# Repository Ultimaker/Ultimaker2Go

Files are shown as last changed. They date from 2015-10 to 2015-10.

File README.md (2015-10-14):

# Ultimaker2Go

Bill of Materials and parts for Ultimaker2Go

In this repository you will find the documentation and source files for all parts in the Ultimaker2Go 3D printer. In the Bill Of Materials (BOM) repository all the parts are numbered and named with the correct amounts. Every part has a separate directory containing all the relevant files. 

The electronic files can be found in the directory 1249 Ulticontroller board and 1546 Ultimainboard V2.1.4.

If you are missing a part or information feel free to file an issue on github.

Harma Woldhuis <br>
Ultimaker Research and Development

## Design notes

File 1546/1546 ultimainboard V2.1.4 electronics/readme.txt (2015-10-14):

The UltiMainboard 2.x.x electronics are released under GPLv2 license.
And are based on the origonal Ultimaker electronics design by Jan-Jaap Schuurman, Siert Wijnia and ErikDeBruijn at http://reprap.org/wiki/Ultimaker's_v1.5.7_PCB
As well as the ArduinoMega2560 by Arduino: http://arduino.cc/en/Main/arduinoBoardMega2560

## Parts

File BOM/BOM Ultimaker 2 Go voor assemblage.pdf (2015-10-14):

9067-A | Ultimaker 2 Go voor assemblage

per 30-12-2014
Total quantity parts | 328
Partnummer | | Name | Quantity
1021 | A | Ball Bearing 688-2RS | 1
1056 | A | Sintered Bushing | 4
1065 | B | Linear Bearing LM6LUU | 2
1069 | A | Tube Coupling Collet | 2
1071 | A | Clamp Clip | 2
1140 | A | Feeder Spring DR2110 | 1
1152 | B | Table Spring D2150 | 3
1156 | A | Z-shaft Cap Bottom | 2
1162 | C | Limit Switch, Blue Wire | 1
1163 | C | Limit Switch, Red Wire | 1
1165 | A | Timing Pulley 5mm Shaft GT2 | 2
1166 | C | Timing Pulley 8mm Shaft GT2 | 8
1167 | D | Timing Pulley Double 8mm Shaft GT2 | 1
1168 | B | Sliding Block Spring | 4
1170 | B | Square Flanged Linear Bearing LMK12LUU | 2
1175 | A | Spacer 8.2x10x3 | 2
1176 | A | Spacer 8.2x10x5 | 2
1177 | A | Spacer 8.2x10x10 | 4
1178 | A | Spacer 8.2x10x25 | 1
1187 | A | Trapezoidal Lead Nut | 1
1188 | A | Timing Belt GT2 200 | 2
| | nuts and bolts
1200 | A | ISO 7380 M3x8 | 4
1201 | C | Washer Large M3 | 12
1202 | B | ISO 7380 M3x10 | 12
1203 | B | ISO 7380 M3x12 | 13
1204 | B | ISO 7380 M3x16 | 28
1206 | B | ISO 7380 M3x20 | 6
1207 | B | ISO 7380 M3x25 | 12
1209 | B | Nut M3 | 1
1211 | A | Set Screw M4x4 | 11
1212 | B | Set Screw M3x3 | 1
1213 | B | DIN 562 Square Nut M3 A2 | 24
1214 | A | ISO 7040 Nut M3 Prev. torque A2 | 13
1217 | A | ISO 7380 M4x10 A2 | 8
1220 | A | Ball Bearing F688-2RS | 8
1241 | B | Motor Spacer UM2 | 2
1244 | A | Knob Front UM2 | 1
1245 | A | Knob Housing UM2 | 1
1247 | A | Display Oled Blue | 1
1249 | A | Ulticontroller Board | 1
1250 | B | SD card 4G | 1

1255 | A | Sliding Block Half UM2 | 8
1256 | A | Build Platform Glass Retainer Back | 4
1257 | B | Knurled Nut Platform | 3
1258 | G | Feeder Part A | 1
1259 | G | Feeder Part B | 1
1264 | D | Feeder Nut Holder | 1
1279 | A | Feeder Ring | 1
1281 | C | Braided Sleeve Clip | 3
1287 | A | Washer M7 | 1
1288 | A | Washer M6 | 3
1301 | D | Integrated nozzle heater block 3mm filament | 1
1306 | B | Hot end holder bottom | 1
1307 | B | Hot end holder top | 1
1308 | B | Cooling Rib Hot End | 1
1310 | A | Hot end Isolator | 1
1311 | A | Spring D2000 | 1
1313 | A | Model Cooling Fan 12VDC 0.1 A | 2
1315 | A | Jumper | 2
1321 | C | Print Head Middle | 1
1322 | D | Print Head Bottom | 1
1330 | B | Hot-end Cooling Fan 5VDC 0.08A | 1
1348 | A | ISO 7380 M3x4 A2 | 4
1351 | A | ISO 4762 M2,5x10 | 2
1354 | A | ISO 724 Hex nut M7 | 1
1355 | B | Heated Bed Bolt 8 mm | 4
1356 | B | Heated Bed Bolt 20 mm | 3
1357 | A | DIN 913 M3x14 | 1
1358 | A | chipboard panel screw 2.5x16 | 8
1363 | A | Ferrite Core | 1
1364 | A | PTFE Isolator Coupler Glass Filled 3.2 mm | 1
1365 | A | Dual Fan Bracket Safety | 1
1366 | A | PTFE nozzle ring | 1
1521 | A | Short Print Head Thumb Screw | 4
1545 | A | Spacer 3.2x6x3 | 2
1546 | A | Ultimainboard V2.1.4 | 1
1701 | B | Y-linear shaft | 2
1702 | B | X-linear shaft | 2
1703 | C | Z-linear shaft | 2
1704 | C | Print Head Shaft X | 1
1705 | C | Print Head Shaft Y | 1
1706 | A | Z-Motor with Trapezoidal Lead Screw | 1
1707 | A | Limit Switch, Black Wire | 1
1710 | A | LED Strip Cold white | 1
1711 | A | Back Panel | 1
1712 | A | Left Panel | 1
1713 | A | Right Panel | 1
1714 | A | Bottom Panel | 1
1715 | A | Top Panel | 1
1716 | A | Front Panel | 1
1717 | C | Print Table Back Cover | 1

1718

A | Short Reel Holder
1
1720 | D | Print Table Base Plate | 1
1722 | A | Print Table Bed | 1
1723 | A | Display Rubber | 2
1730 | A | Double flat Cable 10 Wire | 1
1732 | B | Print Head Cable | 1
1733 | A | Spacer 3.2x6x7 | 4
1736 | A | Timing Belt GT2 430 | 4
1738 | C | Cable Cover | 2
1740 | B | Electronics Cover | 1
1741 | A | X, Y motor | 2
1742 | A | Feeder motor | 1
1745 | B | PT100B sensor | 1
1746 | C | Heater Cartridge 24V 25W | 1
1747 | A | Bowden Tube | 1
1748 | D | Print head top single hole | 1
1814 | feeder knurled wheel long | 1
1816 | feeder idler lever part A | 1
1817 | feeder idler lever part B | 1

1901

B | Controler Electronics Cover
1

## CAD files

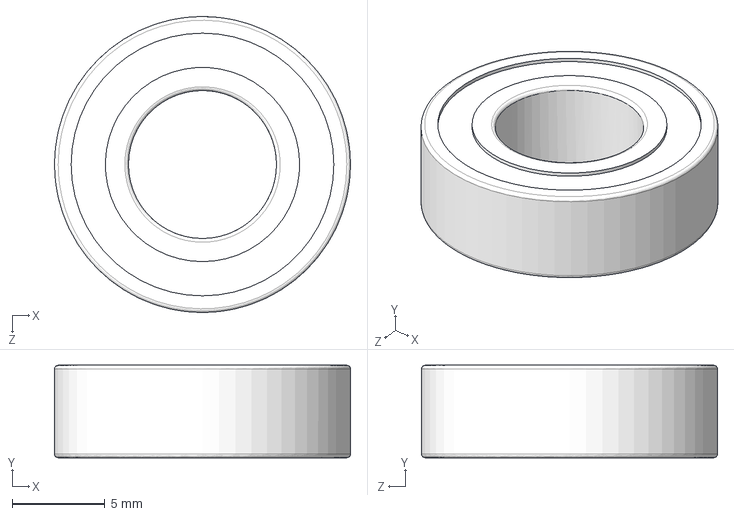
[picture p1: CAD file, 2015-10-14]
1021/1021-Z1P-A.STEP
16.0 x 5.00 x 16.0 mm

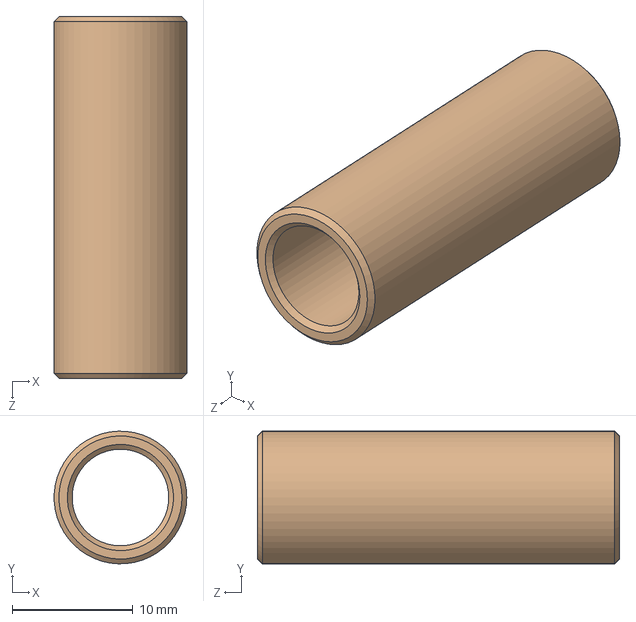
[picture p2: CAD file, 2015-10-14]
1056/1056-A2P-A.STEP
11.0 x 11.0 x 30.0 mm

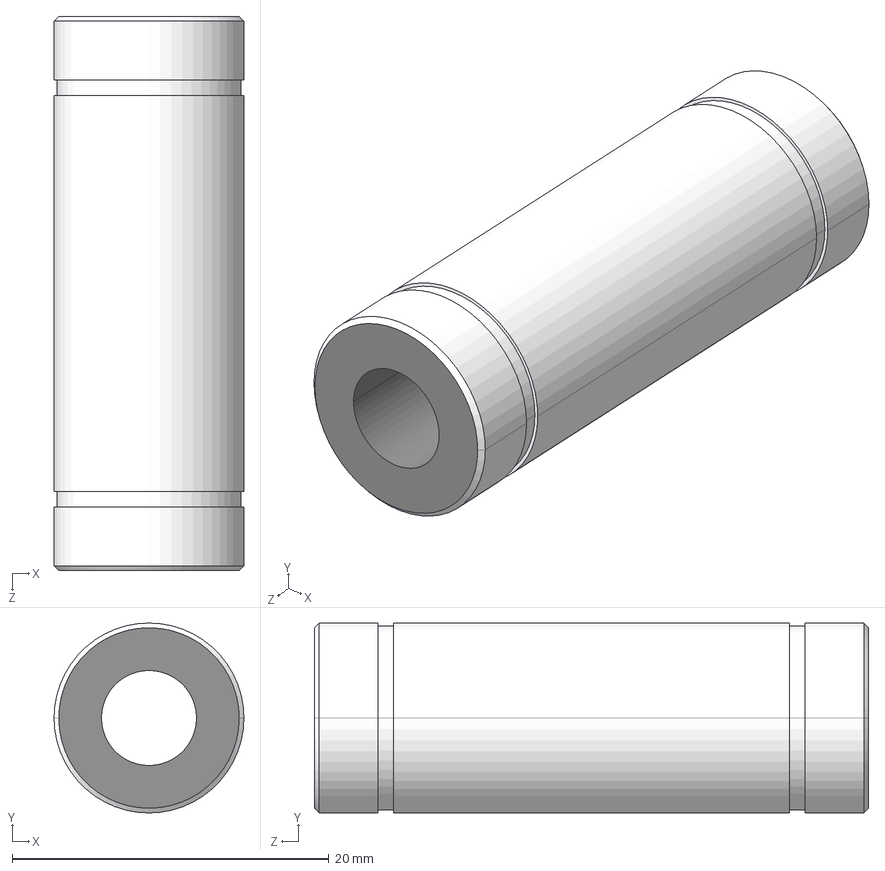
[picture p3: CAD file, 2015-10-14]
1065/1065-Z1P-B.STEP
12.0 x 12.0 x 35.0 mm

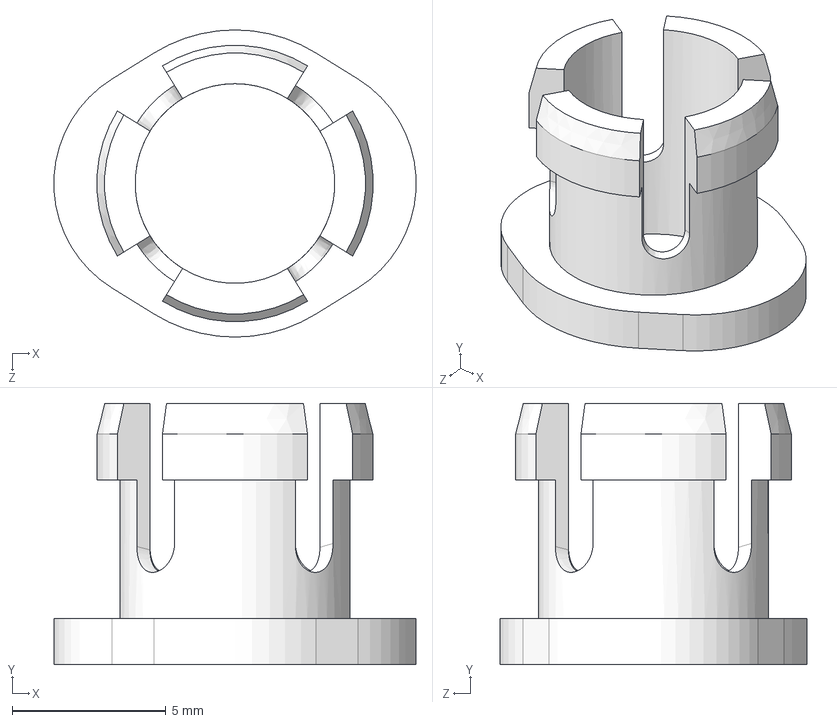
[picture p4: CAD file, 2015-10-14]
1069/1069-Z1P-A.STEP
11.8 x 8.50 x 10.00 mm

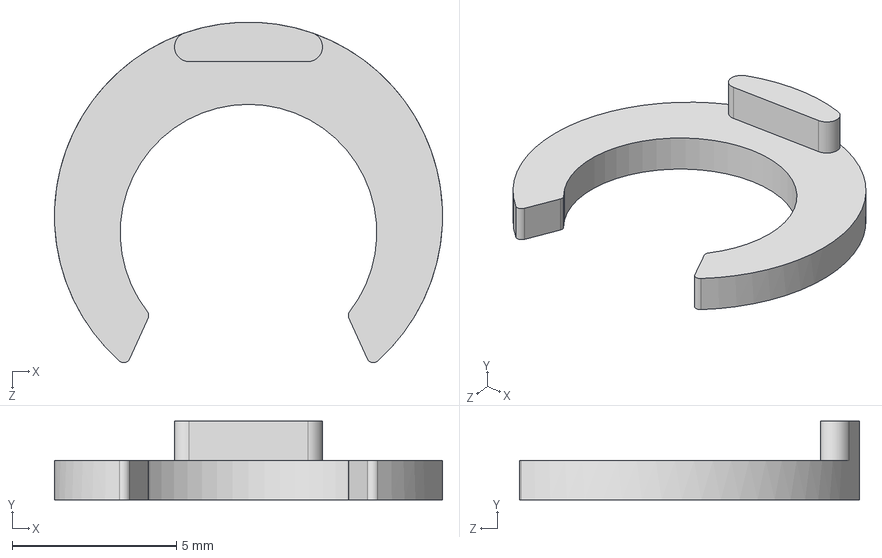
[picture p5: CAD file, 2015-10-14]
1071/1071-Z1P-A.STEP
11.8 x 2.40 x 10.3 mm

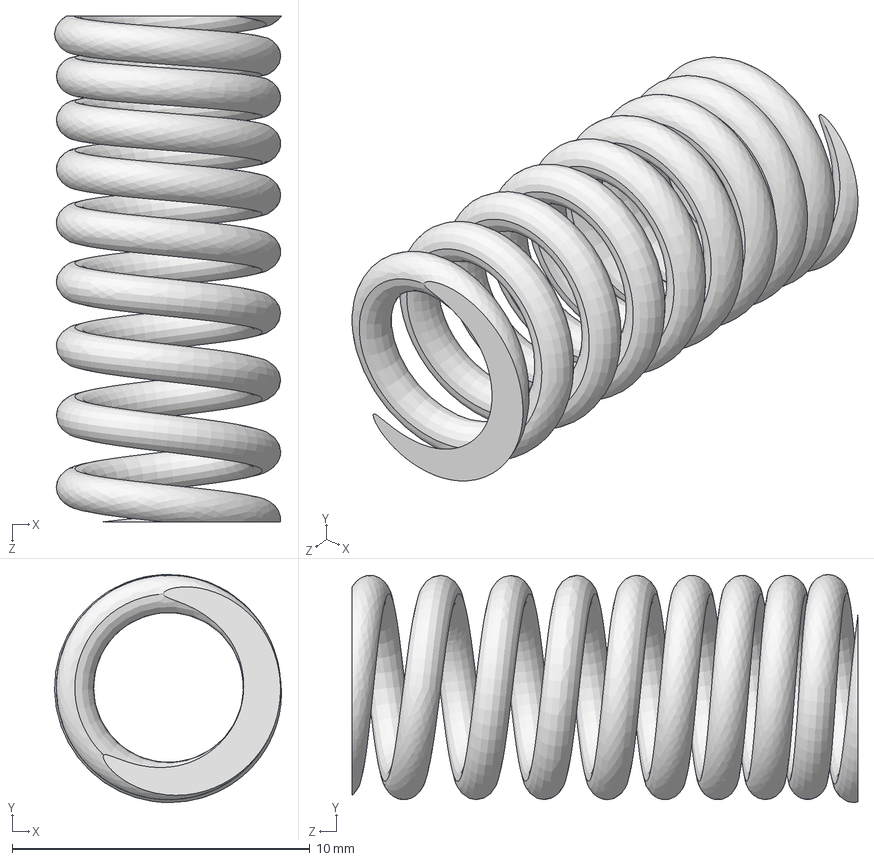
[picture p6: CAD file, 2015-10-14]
1140/1140-01.STEP
7.63 x 7.67 x 17.0 mm

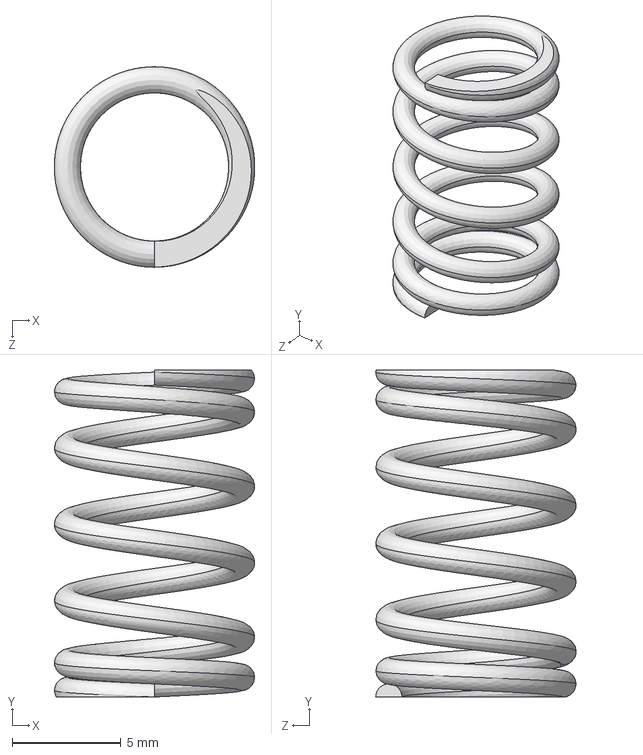
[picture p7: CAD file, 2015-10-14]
1152/1152-B2P-B.STEP
9.20 x 15.0 x 9.20 mm

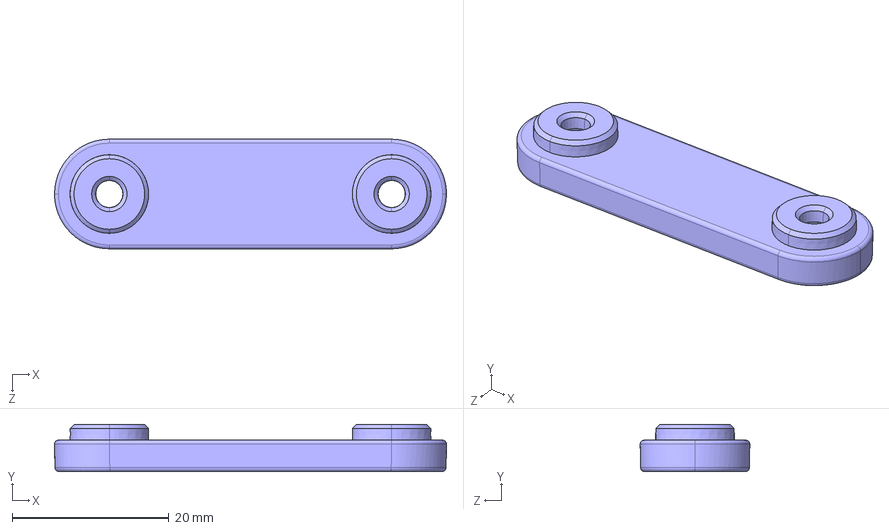
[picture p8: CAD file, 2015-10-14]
1156/1156-B2P-A.STEP
50.0 x 6.00 x 14.0 mm

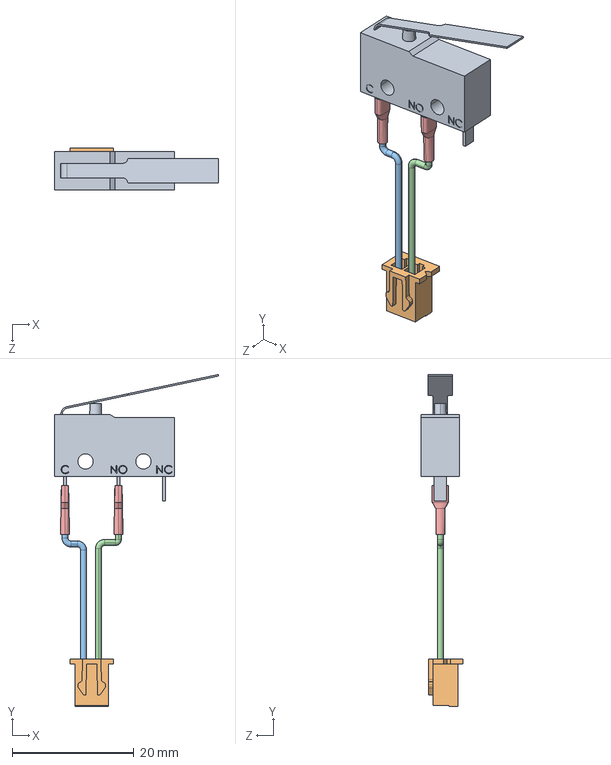
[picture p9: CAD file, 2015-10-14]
1162/1162-Z1P-C.STEP
27.1 x 54.6 x 6.90 mm

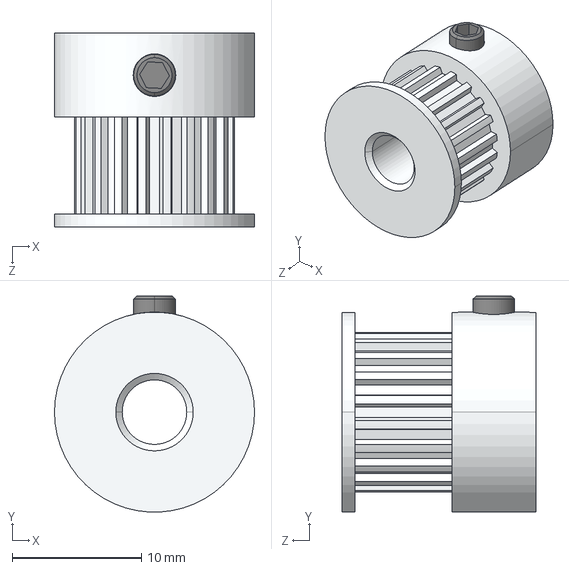
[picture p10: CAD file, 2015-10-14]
1165/1165-B2P-A.STEP
15.5 x 16.7 x 15.0 mm

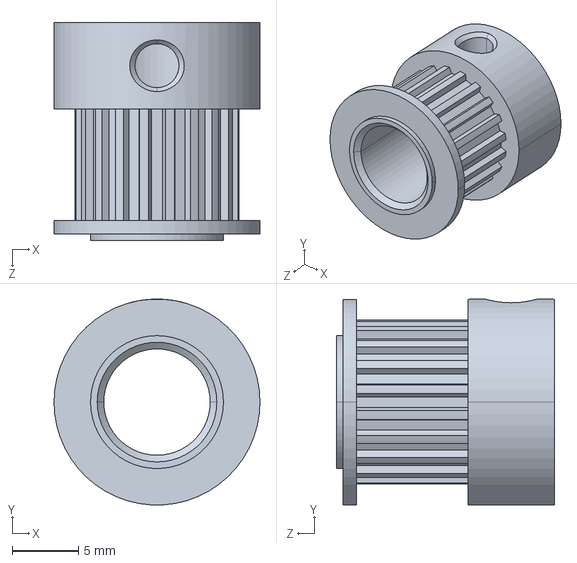
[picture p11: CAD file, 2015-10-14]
1166/1166-C.STEP
15.5 x 15.5 x 16.4 mm

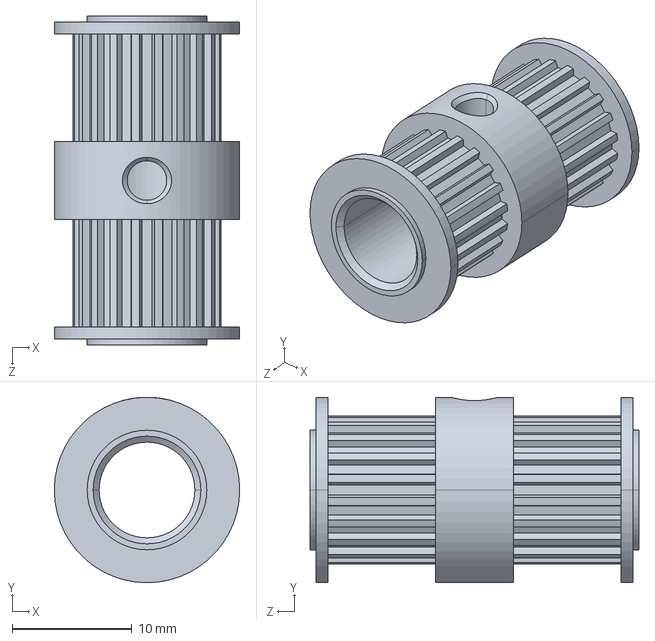
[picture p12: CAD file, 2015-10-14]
1167/1167-D.STEP
15.5 x 15.5 x 27.5 mm

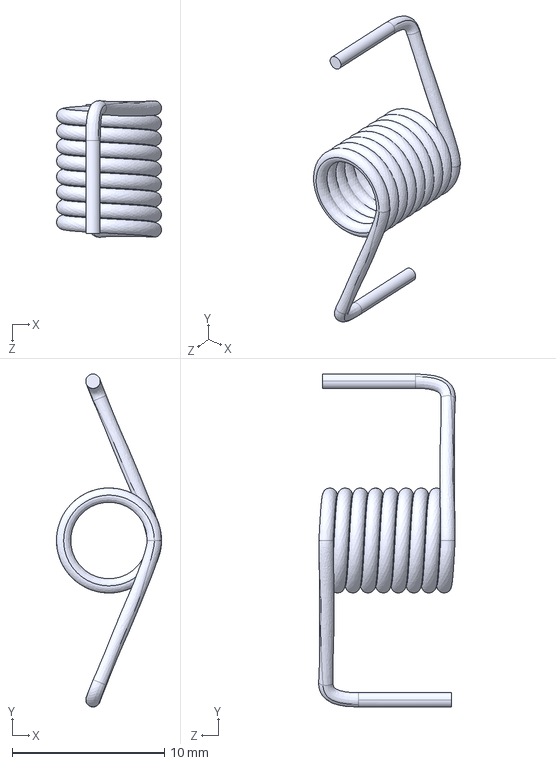
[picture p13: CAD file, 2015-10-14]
1168/1168-B2P-B.STEP
6.91 x 21.9 x 8.98 mm

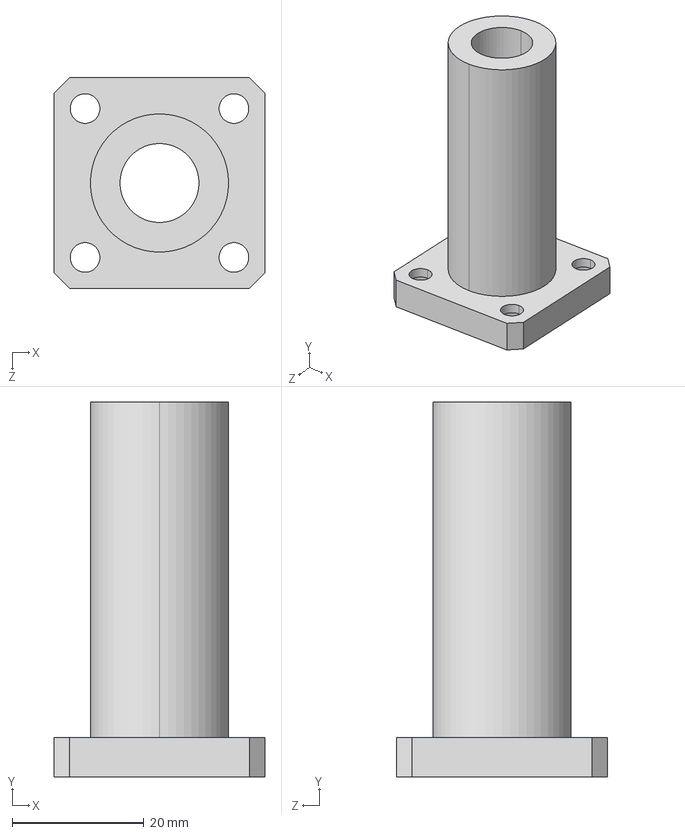
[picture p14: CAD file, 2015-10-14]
1170/1170-B2P-B.STEP
32.0 x 57.0 x 32.0 mm

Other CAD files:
1163/1163-Z1P-C.STEP
1175/1175-A.STEP
1176/1176-B1P-A.STEP
1177/1177-B1P-A.STEP
1178/1178-B1P-A.STEP
1187/1187-B2P-A.STEP
1188/1188-B2P-A.STEP
1200/1200-Z1P-A ISO 7380 M3x8 new.STEP
1201/1201-Z1P-C.STEP
1202/1202-Z1P-B.STEP
1203/1203-Z1P-B.STEP
1204/1204-Z1P-B.STEP
1206/1206-Z1P-B.STEP
1207/1207-Z1P-B.STEP
1209/1209-C.STEP
1211/1211-Z1P-A.STEP
1212/1212-Z1P-B.STEP
1213/1213-Z1P-B.STEP
1214/1214-Z1P-A.STEP
1217/1217-A.STEP
1220/1220-A.STEP
1241/1241-B2P-B.STEP
1244/1244-B2P-A.STEP
1245/1245-B2P-A.STEP
1247/1247-B2P-A.STEP
1250/1250-B.STEP
1255/1255-B2P-A.STEP
1256/1256-B2P-A.STEP
1257/1257-B2P-B.STEP
1258/1258-G.STEP
1259/1259-G.STEP
1264/1264-D.STEP
1279/1279-B2P-A.STEP
1281/1281-B2P-C.STEP
1287/1287-Z1P-A.STEP
1288/1288-Z1P-A.STEP
1301/1301-Z2P-D.STEP
1306/1306-C.STEP
1307/1307-C.STEP
1308/1308-C.STEP
1310/1310-B.STEP
1311/1311-Z2P-A.STEP
1313/1313-A.STEP
1315/1315-Z1P-A.STEP
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

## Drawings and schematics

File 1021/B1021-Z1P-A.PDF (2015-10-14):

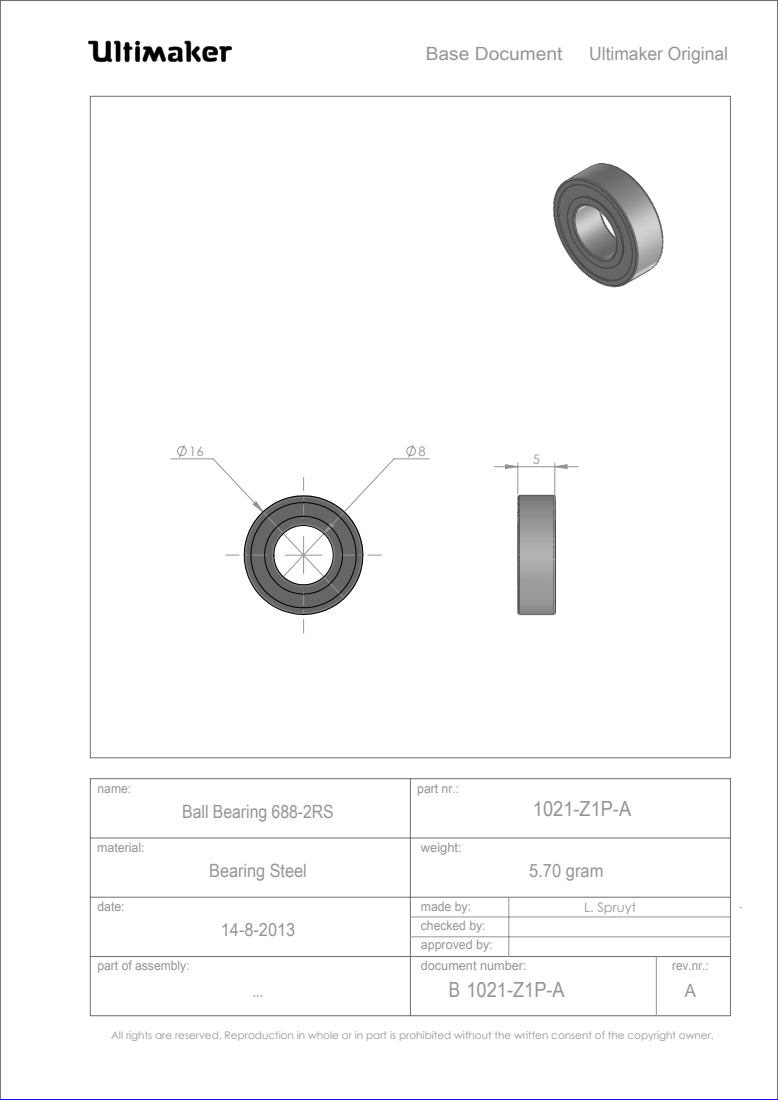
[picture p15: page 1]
Bearing Steel; 5.70 gram; Ball Bearing 688-2RS; Ultimaker Original; part of assembly:; rev.nr.:; part nr.:; made by:; Base Document; approved by:; checked by:; L. Spruyt; document number: B 1021-Z1P-A

All rights are reserved. Reproduction in whole or in part is prohibited without the written consent of the copyright owner.

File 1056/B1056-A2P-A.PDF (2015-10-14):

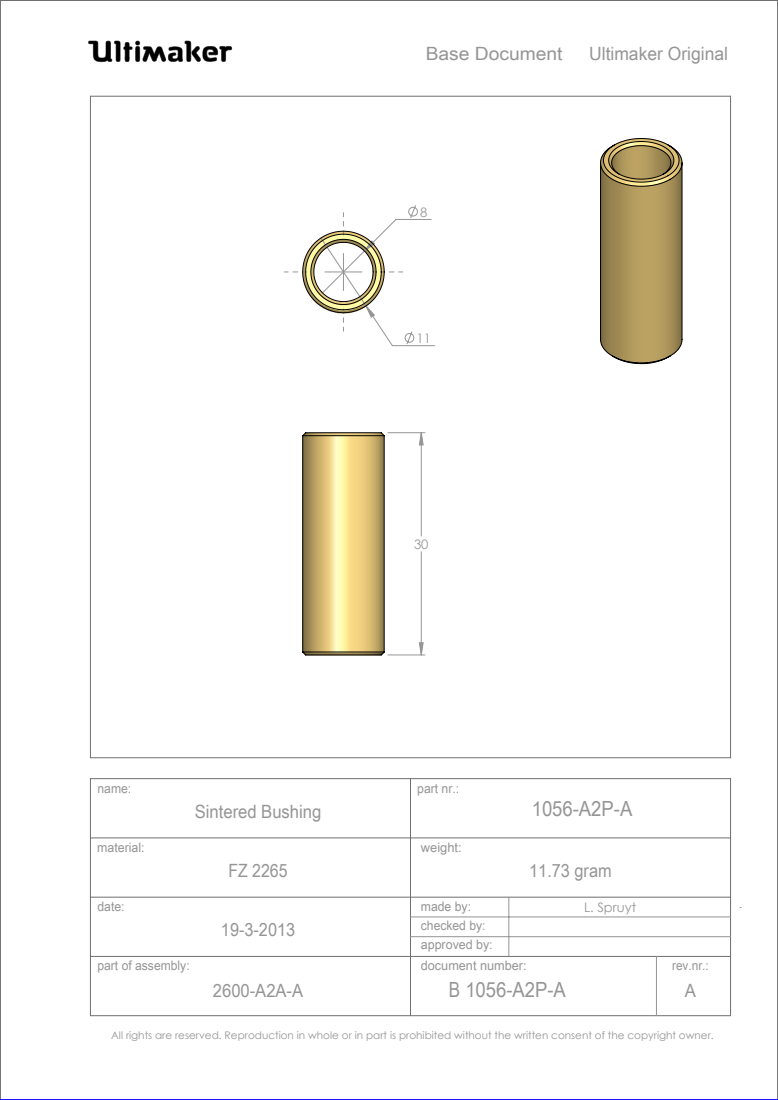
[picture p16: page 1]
11.73 gram; Sintered Bushing; Ultimaker Original; part of assembly:; rev.nr.:; part nr.:; made by:; Base Document; approved by:; checked by:; L. Spruyt; document number: B 1056-A2P-A

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

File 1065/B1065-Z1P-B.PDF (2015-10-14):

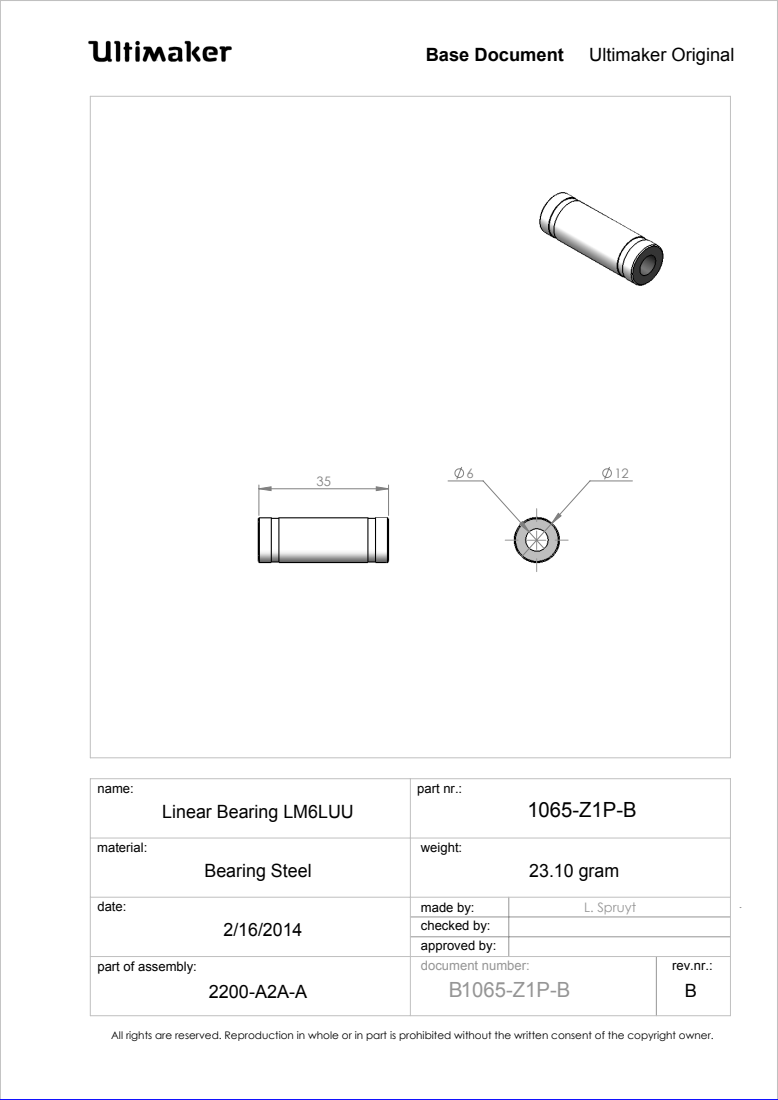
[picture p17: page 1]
Bearing Steel; 23.10 gram; Linear Bearing LM6LUU; Ultimaker Original; part of assembly:; rev.nr.:; part nr.:; made by:; Base Document; approved by:; checked by:; L. Spruyt; document number:

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

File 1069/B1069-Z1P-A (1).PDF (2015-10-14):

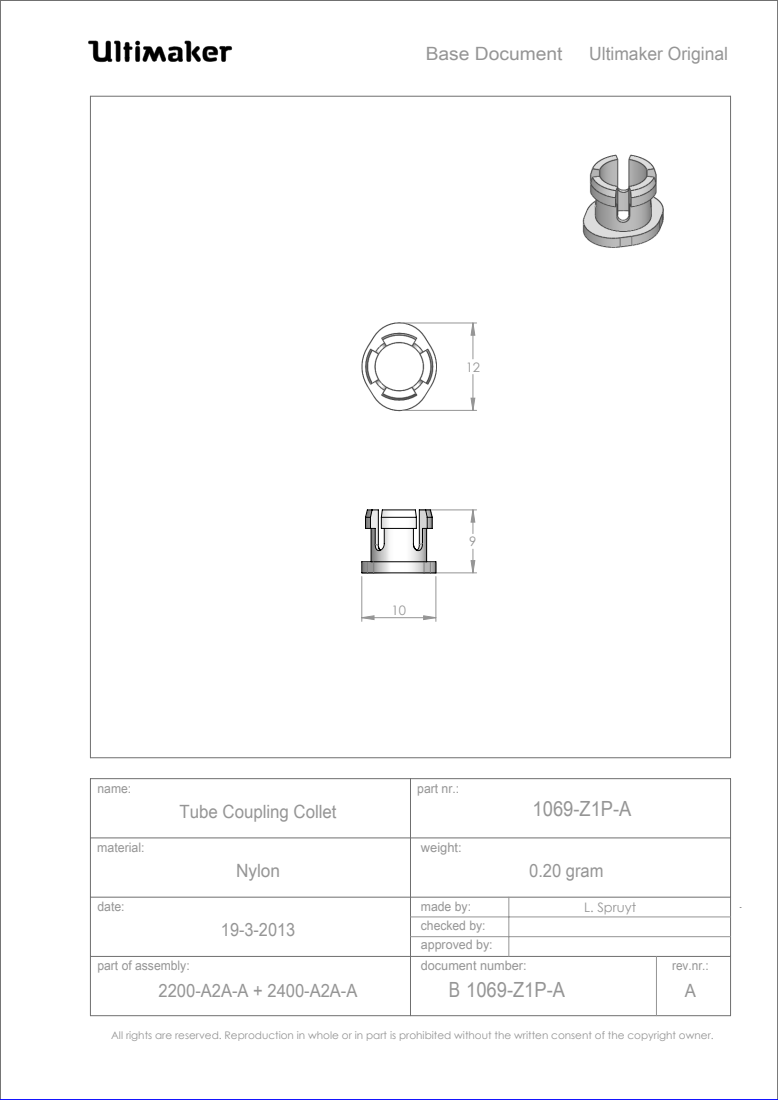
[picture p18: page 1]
Nylon; 0.20 gram; Ultimaker Original; part of assembly:; rev.nr.:; part nr.:; made by:; Base Document; approved by:; checked by:; L. Spruyt; document number: B 1069-Z1P-A

Tube Coupling Collet

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

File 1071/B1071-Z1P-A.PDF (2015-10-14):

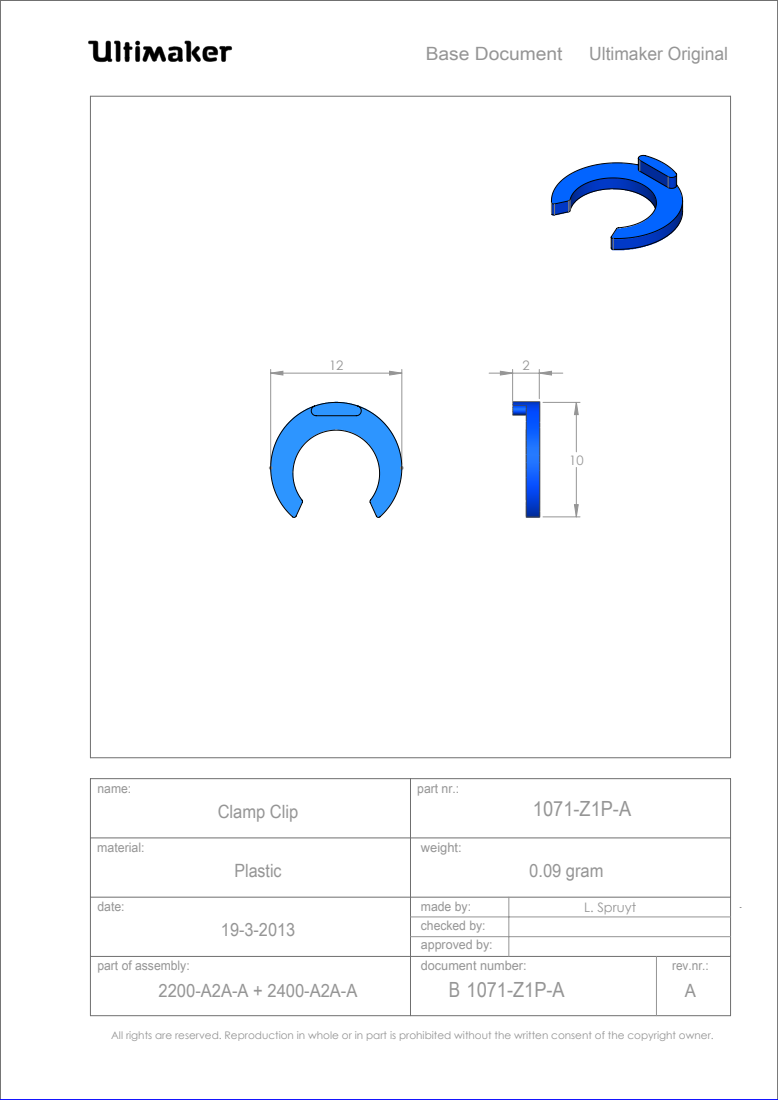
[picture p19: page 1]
Plastic; 0.09 gram; Clamp Clip; Ultimaker Original; part of assembly:; rev.nr.:; part nr.:; made by:; Base Document; approved by:; checked by:; L. Spruyt; document number: B 1071-Z1P-A

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

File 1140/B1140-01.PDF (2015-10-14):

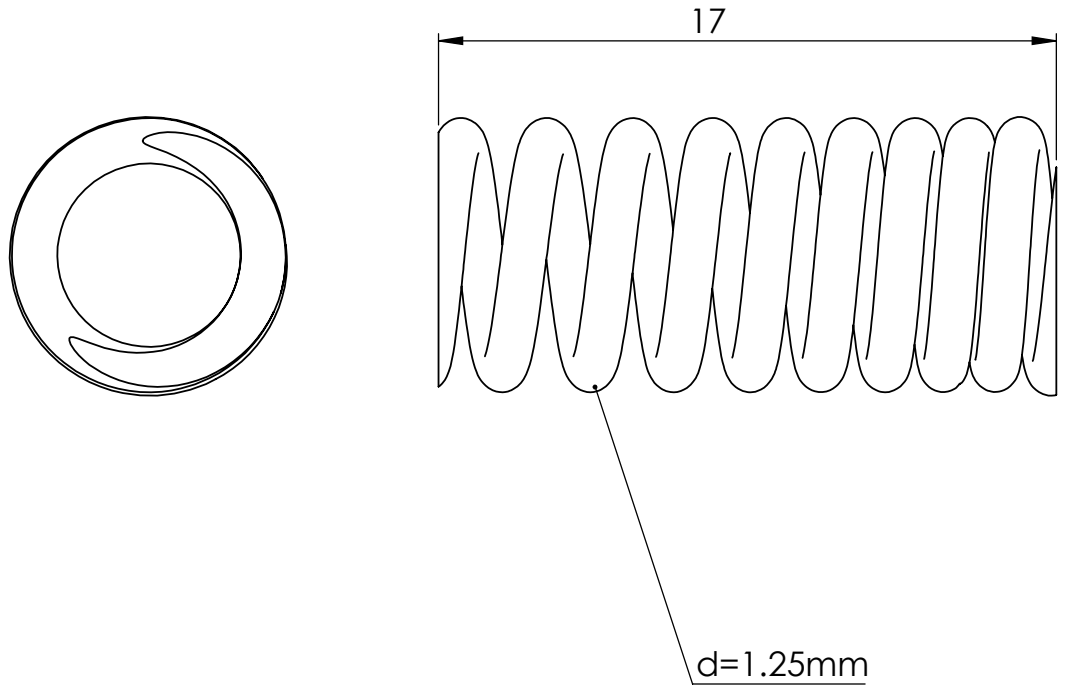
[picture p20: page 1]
Part Nr.: 1143-01; Product: Ultimaker 2

Burgemeester R. vd Venlaan
4191PL Geldermalsen
The Netherlands

Drawn: Ivar Kraaijevanger | Checked by: **** | Description: Feeder Spring DR2110

American Projection | Scale: 5:1 (A4) | Approved by: ****

Units: mm. | Material: Stainless Steel, DIN 17.224 | Released for prototyping: Yes
Date: 24-11-2014 | Norm: DIN 2095-2 | Released for null-series: Yes
Sheet number: 2 of 2 | Amount: 1 | Released for production: Yes

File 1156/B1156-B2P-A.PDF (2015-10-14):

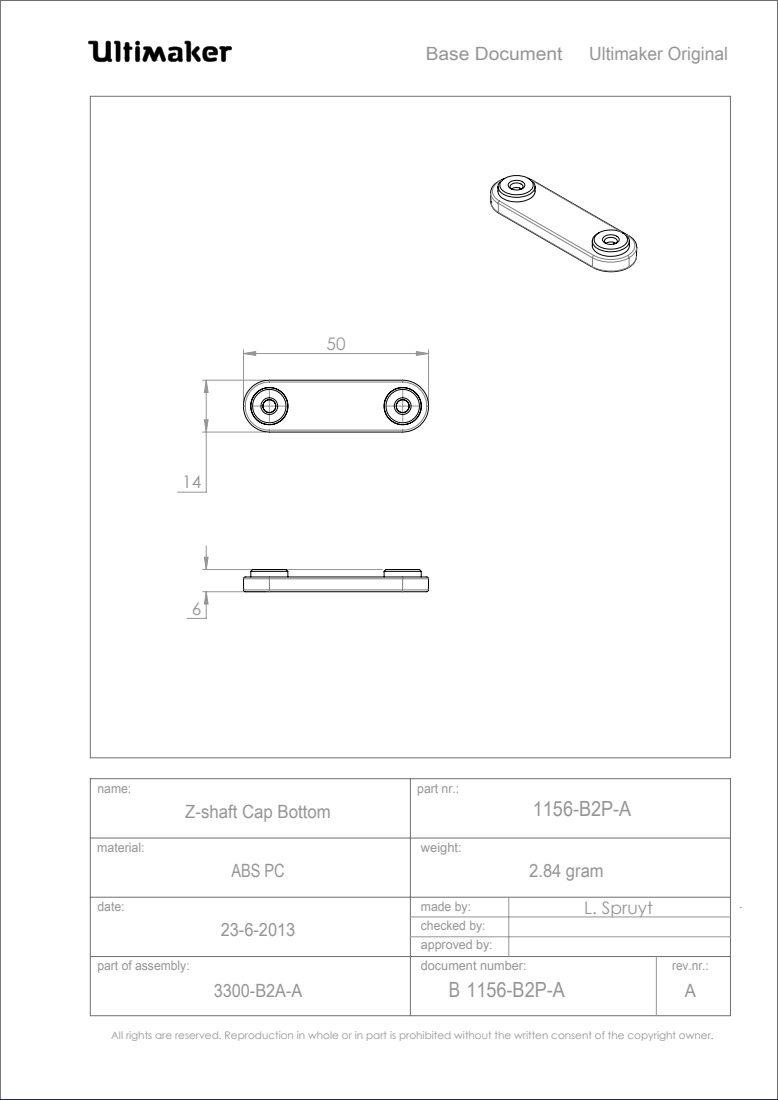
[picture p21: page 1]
ABS PC; 2.84 gram; Ultimaker Original; part of assembly:; rev.nr.:; part nr.:; made by:; Base Document; approved by:; checked by:; L. Spruyt; document number: B 1156-B2P-A

Z-shaft Cap Bottom

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

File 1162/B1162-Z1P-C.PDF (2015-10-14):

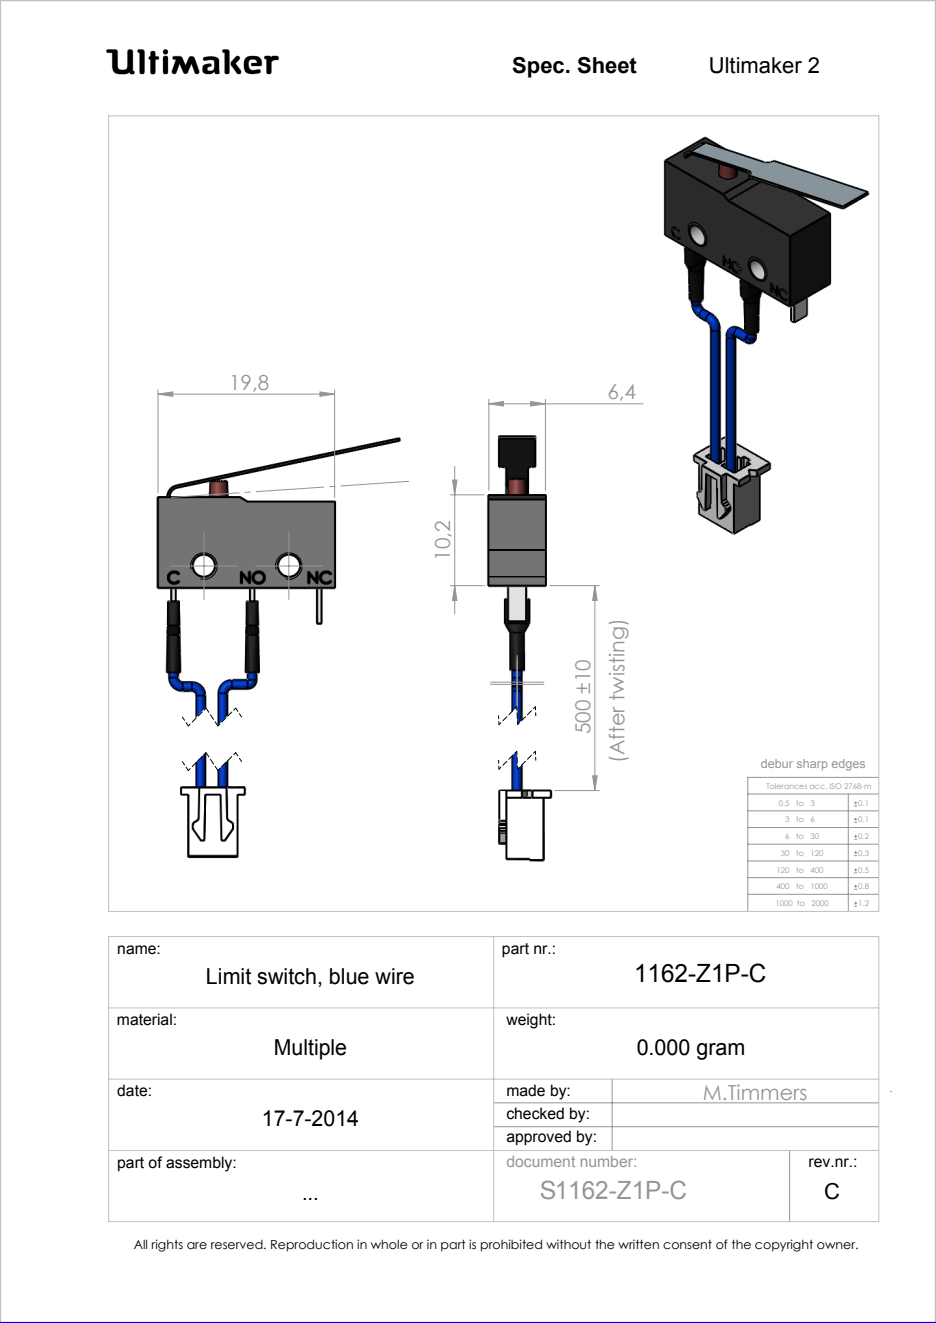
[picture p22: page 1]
500 ±10 (After twisting); Multiple; 0.000 gram; Ultimaker 2; part of assembly:; rev.nr.:; part nr.:; made by:; Spec. Sheet; approved by:; checked by:; document number:; Tolerances acc. ISO 2768-m

debur sharp edges

Limit switch, blue wire

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

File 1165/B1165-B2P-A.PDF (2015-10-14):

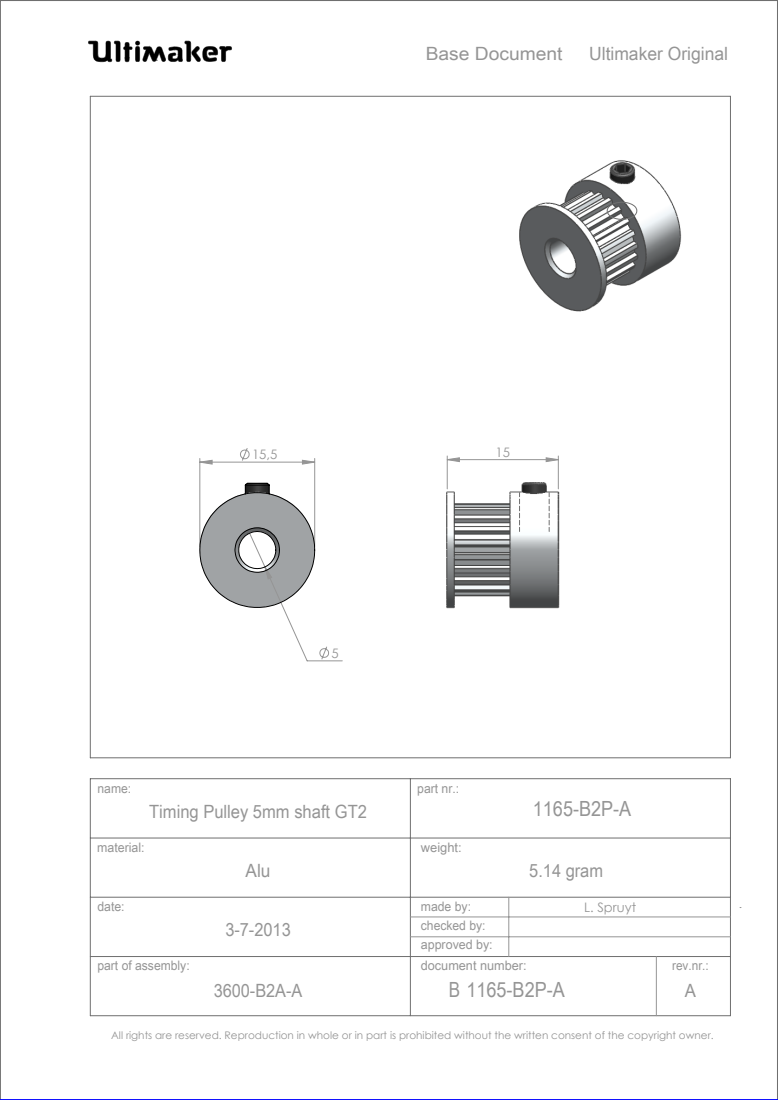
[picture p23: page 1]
Alu; 5.14 gram; Ultimaker Original; part of assembly:; rev.nr.:; part nr.:; made by:; Base Document; approved by:; checked by:; L. Spruyt; document number: B 1165-B2P-A

name:
Timing Pulley 5mm shaft GT2

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

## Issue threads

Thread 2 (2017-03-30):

BOM Ultimaker 2 Go voor assemblage.pdf

traiger, 2017-03-30:
In the BOM could you cite the specific length of the bowden tube for the Ultimaker 2 Go? I can't find it anywhere.

Closed 2017-03-30.
